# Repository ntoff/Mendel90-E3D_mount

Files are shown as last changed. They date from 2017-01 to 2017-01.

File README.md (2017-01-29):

# Mendel90 E3D Direct Drive Mount

Printable mount for an E3D hotend on a Mendel90 reprap printer.

Uses some of the parts from the Orca printer's extruder and mount system
http://reprap.org/wiki/Orca
http://reprap.org/wiki/Orca_alternative_build

Note: Screw length may vary depending how thick you tell it to make the plates.
You may be required to shave some off one of the bolts if it interferes with the E3D fan
since bolts of odd lengths (like M4 x 13mm) may not exist.

## BOM:

## Idler / feeder bit:
M4 x 70 (x4)
M4 washers (x8)
4.5 - 5mm ID springs 20mm long
M4 x 45 (x2)
M4 nyloc nuts (x2)

## Idler bearing holder
M4 rod approx. 18mm long
M4 washers (x2)
Bearing w/ 4mm hole 13mm OD 5mm wide
M4 nyloc nuts (x4)

## Motor mount:
M3 x8 (x4)
M4 x15 (x1)
M3 washers (x4)
M4 washers (x2)
M4 nyloc nuts (x1)

## Base:
M4 x 15 countersunk (x4)
M4 washers (x2)
M4 nyloc nuts (x4)

driverholder.STL vs extruder guide2.stl: driverholder includes an extra mount point on the base, makes it stronger but also makes it harder to remove / mount. 
I suggest sticking with the guide2 version.

Obviously don't print the shaft, bearing, or bearing real files, they were just for reference for design, I took some artistic liberty with the size of the bearing,
stl dimensions are not an accurate representation of any actual bearing sizes.

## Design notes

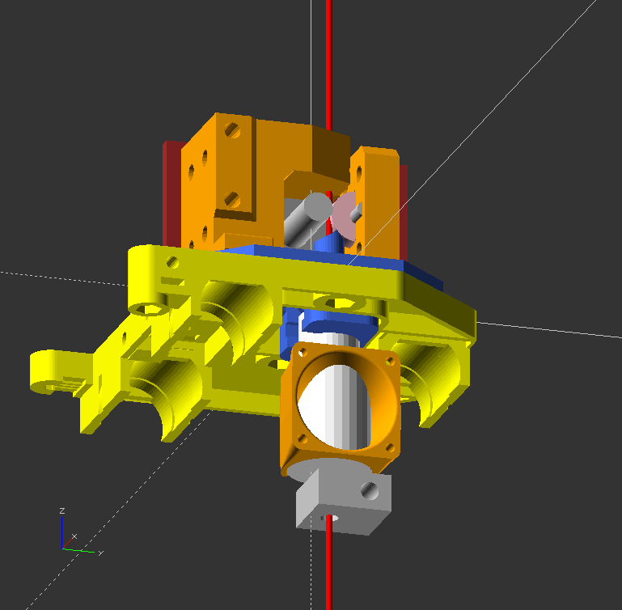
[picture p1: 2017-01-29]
e3d mount.png

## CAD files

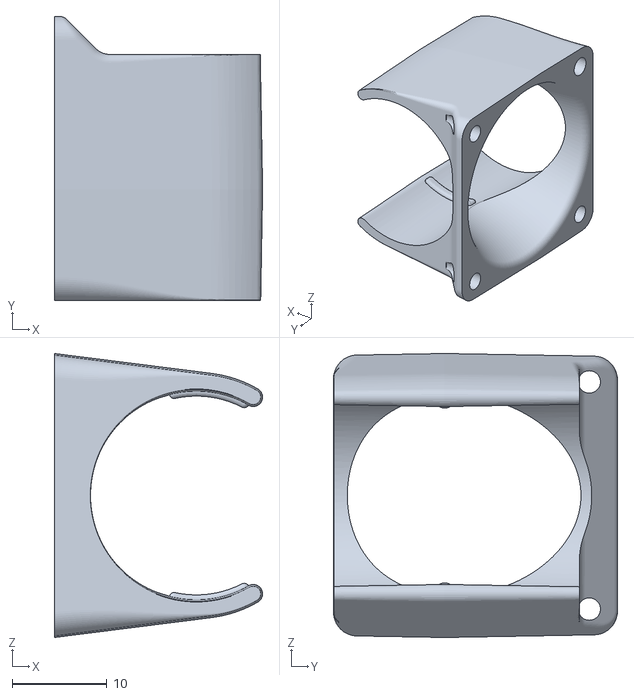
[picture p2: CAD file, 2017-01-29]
V6.6_Duct.stl
22.0 x 30.0 x 30.0

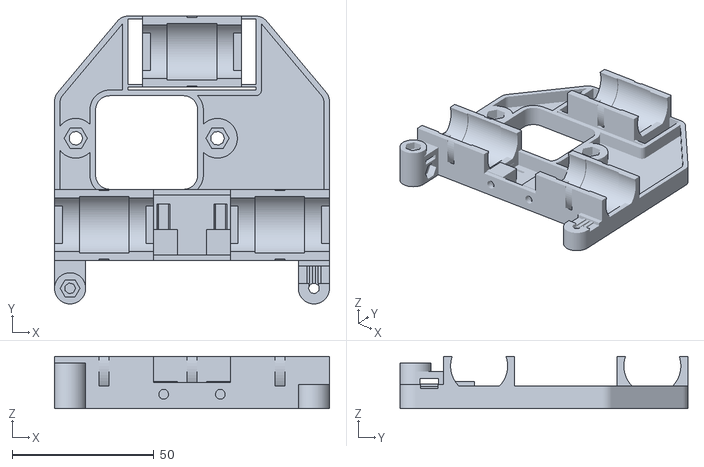
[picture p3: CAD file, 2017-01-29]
x_carriage.stl
97.0 x 101.5 x 18.4

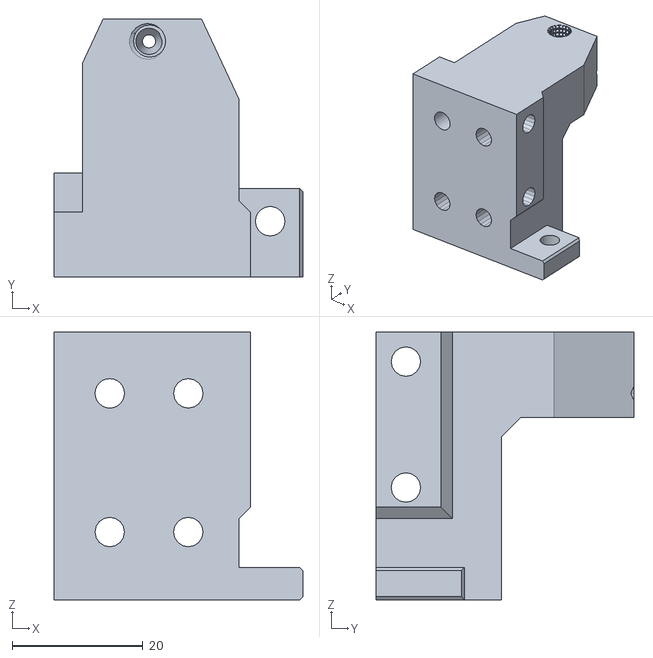
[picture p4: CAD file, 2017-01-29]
driverholder.STL
38.0 x 39.4 x 40.9

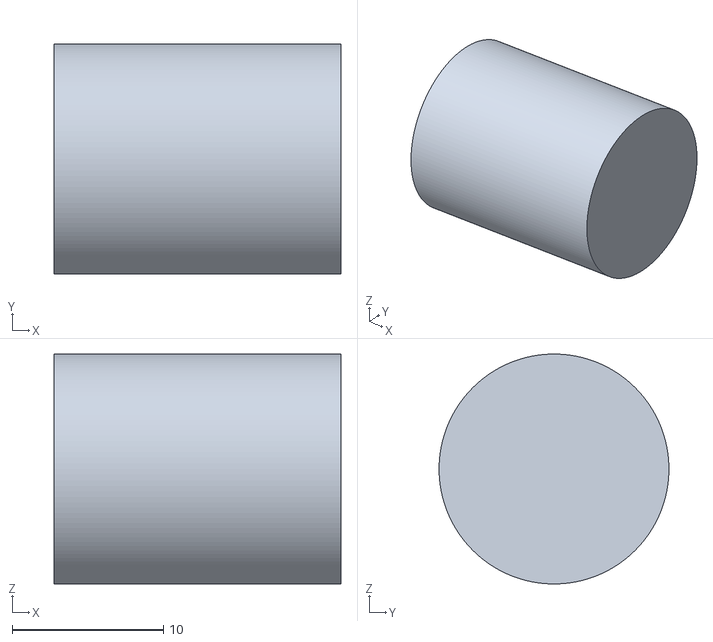
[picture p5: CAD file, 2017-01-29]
idler_bearing.stl
19.0 x 15.2 x 15.2

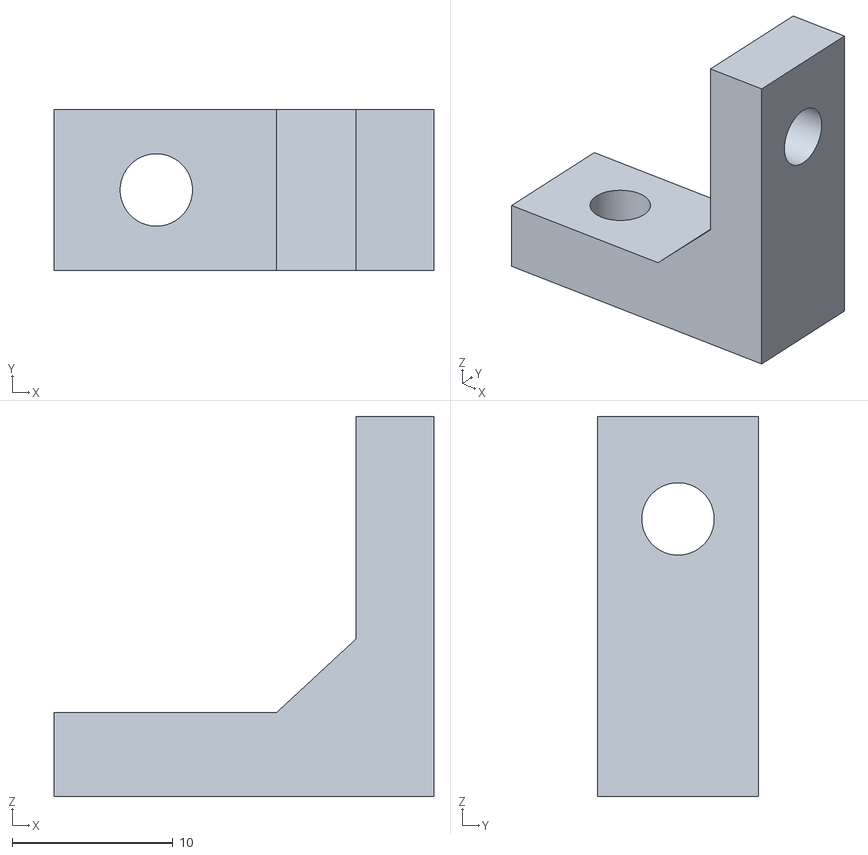
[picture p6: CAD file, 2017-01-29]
extruder_corner.stl
23.6 x 10.0 x 23.7

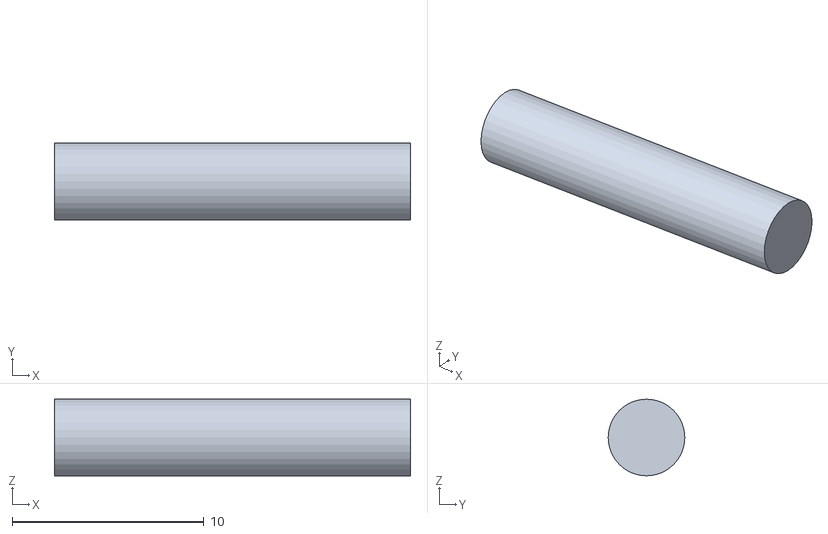
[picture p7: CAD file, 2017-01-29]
idler_shaft.stl
18.6 x 4.00 x 4.00

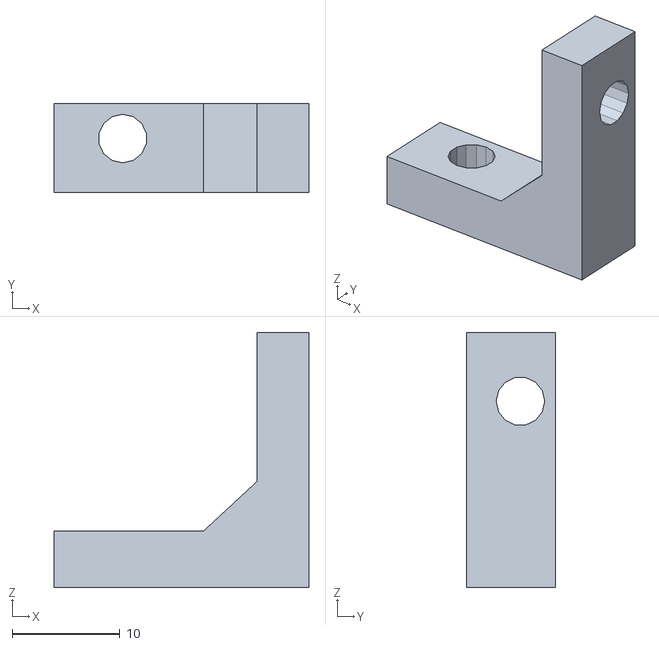
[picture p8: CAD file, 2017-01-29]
extruder_corner_shaved.stl
23.6 x 8.25 x 23.7

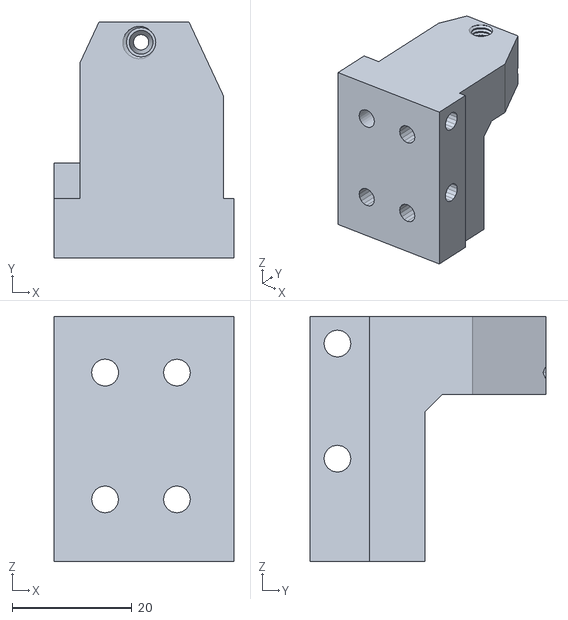
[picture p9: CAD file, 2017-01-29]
extruder guide2.stl
30.0 x 39.4 x 40.9

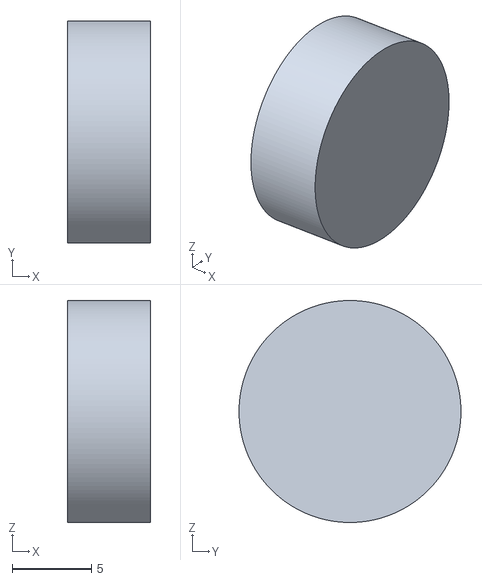
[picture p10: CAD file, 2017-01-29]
idler_bearing_real.stl
5.24 x 14.0 x 14.0

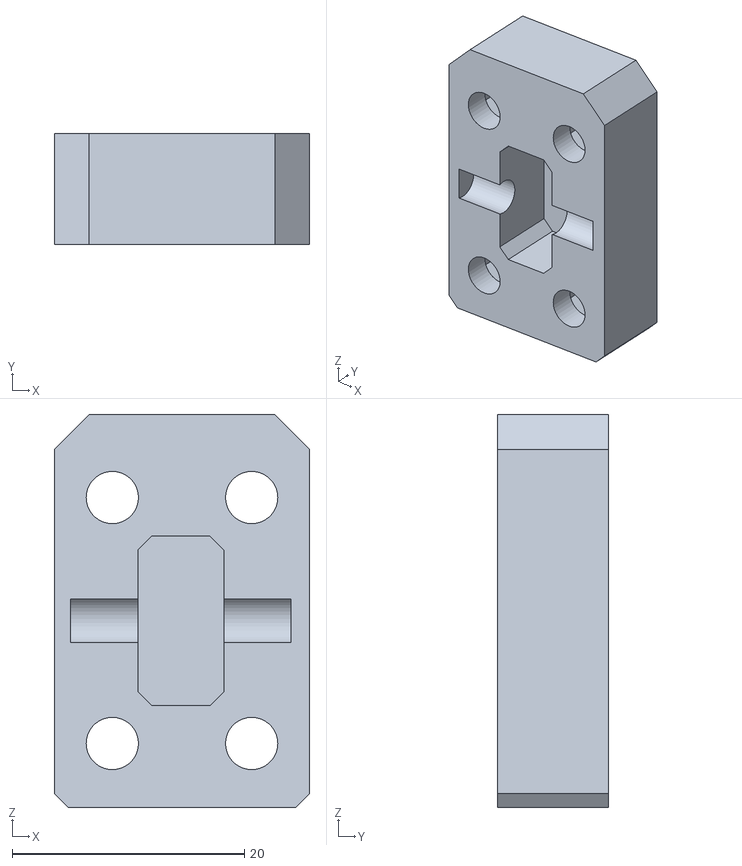
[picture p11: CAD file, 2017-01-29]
idler.stl
22.0 x 9.52 x 33.8

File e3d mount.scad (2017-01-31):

include<nema17.scad>
/*E3D mount for a mendel90
F5 to compile it for viewing the assembled assembly
F6 to compile it with just the mount plate, base plate, and filament guide to see orientation of parts

change print variable to 1 and F6 to compile for printing

note: Only openscad parts are compiled for printing, imported STLs won't show up but can be manually
added to your slicer. DO NOT PRINT THE X CARRIAGE, included x carriage is only for design reference,
the x carriage generated for your machine should be used as long as the holes all line up, check by
replacing the included x carriage with your own.
*/

//CHANGE THIS TO 1 TO COMPILE FOR PRINTING
print=0;
$fn=32;
plate_thickness=5;
upright_thickness=4;
offset=5; //moves the motor left and right for different sized drive wheels
x=18.5;
y=35;
y2=31;
plate_height=43;
filament_hole_size = 17; //size of the hole in the base plate, NOT the size of your filament
bowden_tube_dia=4.5; //diameter of the PTFE liner in the e3d

module extras(){
    %color("red")translate([0,5,-100])cylinder(d=1.75,h=200); //filament for reference
    /**/
    %color("white")translate([0,5,-42.7-3]){
        cylinder(d=22.3,h=26);
        cylinder(d=16,h=42.7);
        translate([0,0,-7.1])cylinder(d=3,h=7.1);
        translate([0,0,-7.1])cylinder(d=3,h=11.5);
        } //e3d heatsink for reference
    %color("silver")translate([0,4+5,-42.7-3-8])
        difference(){
            cube([20,20,10],center=true);
            translate([0,4,0])rotate([0,90,0])cylinder(d=5,h=21,center=true);
            translate([0,-4,0])cylinder(d=5,h=11,center=true);
        }
    /**/
    %translate([-18.52,-0+5-31/2-offset,41.6-(5-plate_thickness)])rotate([0,90,0])nema(nema_height=3,shaft_dia=8);
    %color("red")translate([-18.5,-31.45,plate_thickness])import("extruder_corner_shaved.stl");
    %color("red")translate([-18.5,21.5,plate_thickness])import("extruder_corner.stl");
    %color("orange")translate([18.5,-28+5.5+2.9,plate_thickness])rotate([0,0,0])import("idler.stl"); //idler bearing holder
    %color("silver")translate([18.5,-28+5.5+2.9,plate_thickness])rotate([0,0,0])import("idler_shaft.stl"); //idler bearing holder
    %color("pink")translate([18.5,-28+5.5+2.9,plate_thickness])rotate([0,0,0])import("idler_bearing_real.stl"); //idler bearing holder
    /*
        Comment out ONE of these to make more sense of it all
        either the one with or without the extra tab is needed but not both.
        There's not much difference other than one extra bolt.
    */
    //filament guide with extra mount tab
    //%color("orange")translate([18.5,-28+5.5,plate_thickness])rotate([0,0,0])import("driverholder.stl"); 
    //filament guide without extra mount tab
    %color("purple")translate([18.5,-28+5.5,plate_thickness])rotate([0,0,0])import("extruder guide2.stl"); 
    %color("yellow")translate([0,0,0])rotate([0,180,0])import("x_carriage.stl");
    /*
        E3d fan duct for reference, comment out TWO of them to leave the one you want
    */
    //front facing
    //%color("red")translate([0,5,-19.7])rotate([-90,0,90])import("V6.6_Duct.stl");  
    //right facing
    %color("orange")mirror([1,0,0])translate([0,5,-46])rotate([90,0,0])import("V6.6_Duct.stl"); 
    //left facing
    //%color("green")translate([0,5,-46])rotate([90,0,10])import("V6.6_Duct.stl");
}

module e3d(){
    extra=8;
    hull(){
        translate([0,5,0])rotate([180,0,0])cylinder(d=16.5,h=4);
        translate([0,-5,0])rotate([180,0,0])cylinder(d=16.5,h=4);
    }
    translate([0,5,-3.95+extra])rotate([180,0,0])cylinder(d=12.2,h=6+extra);
    hull(){
        translate([0,5,-3.95+extra])rotate([180,0,0])cylinder(d=11,h=6+extra);
        translate([0,-5,-3.95+extra])rotate([180,0,0])cylinder(d=13,h=6+extra);
    }
    hull(){
        translate([0,5,-10])rotate([180,0,0])cylinder(d=16.5,h=2);
        translate([0,-5,-10])rotate([180,0,0])cylinder(d=16.5,h=2);
    }
}

module baseplate(){
    color("RoyalBlue")difference(){
        union(){
            linear_extrude(plate_thickness)
               polygon( points=[[-45,-y],[-60,-15],[-60,10],[-43,y2],[17,y2],[30,y2-15],[30,-y+10],[20,-y]]);
            minkowski(){
            translate([-25/2,10,0])rotate([180,0,0])cube([25,10,5]);
                rotate([180,0,0])cylinder(d=9,h=5);
            }
            //translate([0,5,0])rotate([180,0,0])cylinder(d=20,h=10,$fn=$fn*2);
        }

        //mounting holes
        translate([-25,0,plate_thickness-2.9])cylinder(d1=5,d2=9,h=3); //countersink
        translate([25,0,plate_thickness-2.9])cylinder(d1=5,d2=9,h=3); //countersink
        translate([-25,0,-1])cylinder(d=5,h=plate_thickness); 
        translate([25,0,-1])cylinder(d=5,h=plate_thickness);
        //end mounting holes
            
        translate([18.5,-28+5.5,1])cylinder(d=5,h=plate_thickness); //guide mount hole
        translate([18.5,-28+5.5,-0.1])cylinder(d1=9,d2=5,h=3); //guide mount hole countersink
        translate([-35.7,-26.25,1])cylinder(d=5,h=plate_thickness); //motor 90 degree bracket mount hole
        translate([-35.7,26.25,1])cylinder(d=5,h=plate_thickness); //motor 90 degree bracket mount hole
        translate([-35.7,-26.25,-0.1])cylinder(d1=9,d2=5,h=3); //motor 90 degree bracket mount hole countersink
        translate([-35.7,26.25,-0.1])cylinder(d1=9,d2=5,h=3); //motor 90 degree bracket mount hole countersink
        
        translate([0,5,+plate_thickness/2])cylinder(d=filament_hole_size,h=plate_thickness+0.5,center=true,$fn=32); //filament hole
        translate([0,0,-3])e3d();

    }
}

module filament_inlet(){
    clearance = 0.4;
    color("RoyalBlue")
    difference(){
        union(){
            translate([0,5,+plate_thickness/2])cylinder(d=filament_hole_size-clearance,h=plate_thickness+0.5,center=true,$fn=32); //filament hole
            translate([0,5,0])cylinder(d=8,h=24,center=false,$fn=32); //filament hole
        }
        translate([18.5,-28+5.5+2.9,plate_thickness])rotate([0,0,0])import("idler_bearing.stl"); //idler bearing holder
        translate([-18.52,-0+5-31/2-offset,40.6])rotate([0,90,0])nema(nema_height=3,shaft_dia=15);
        translate([0,5,0])cylinder(d=bowden_tube_dia,h=25,center=false,$fn=32); //filament hole
        translate([0,5,+plate_thickness/2-0.76])cylinder(d1=filament_hole_size-clearance-2,d2=bowden_tube_dia,h=plate_thickness+0.5-1.5,center=true,$fn=32); //filament hole
    }
}

module nema_mount(){
difference(){
    union(){
        
        color("brown")translate([0,0,plate_thickness])
            linear_extrude(plate_height)
                polygon( points=[[-x,-y],[-x,y2],[-x+upright_thickness,y2],[-x+upright_thickness,-y]]);
        }
     
    translate([-18.52,-0+5-31/2-offset,41.6-(5-plate_thickness)])rotate([0,90,0])nema(nema_height=10);
    //bolt holes
    color("green") translate([0,-26.44,22.17-(5-plate_thickness)])rotate([0,90,0])cylinder(d=5,h=100,center=true);
    color("green") translate([0,26.44,22.17-(5-plate_thickness)])rotate([0,90,0])cylinder(d=5,h=100,center=true);
    color("green") translate([0,-26.44,22.17+19.25-(5-plate_thickness)])rotate([0,90,0])cylinder(d=5,h=100,center=true);
    //zip tie hole for holding the cables, comment out if you don't want it
    color("green") translate([0,26.44,22.17+19.25-(5-plate_thickness)])rotate([0,90,0])cylinder(d=5,h=100,center=true);
}
}

if (print == 1){
    translate([0,0,plate_thickness])rotate([180,0,0]) 
        baseplate();
    translate([-10,35,-x+upright_thickness])rotate([0,90,90]) 
        nema_mount();
    translate([-8,56,0.25]) 
        filament_inlet();
}else {
    baseplate();
    nema_mount();
    filament_inlet();
    extras();
    }

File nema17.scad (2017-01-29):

nema_height=10;
shaft_dia=6;
module nema(nema_height,shaft_dia){
    echo("Note: Nema is designed to be differenced out of something, dimensions of screws and shaft are larger than actual");
linear_extrude(nema_height){
    hull(){
        translate([0,0-2,0])circle(d=3.5,$fn=16);
        translate([0,02,0])circle(d=3.5,$fn=16);
    }
    hull(){
        translate([31,0-2,0])circle(d=3.5,$fn=16);
        translate([31,02,0])circle(d=3.5,$fn=16);
    }
    hull(){
        translate([31,31-2,0])circle(d=3.5,$fn=16);
        translate([31,31+2,0])circle(d=3.5,$fn=16);
    }
    hull(){
        translate([0,31-2,0])circle(d=3.5,$fn=16);
        translate([0,31+2,0])circle(d=3.5,$fn=16);
    }
}
linear_extrude(nema_height)hull(){
    translate([31/2,31/2-2,0])circle(d=25);
    translate([31/2,31/2+2,0])circle(d=25);
}
color("Silver")translate([31/2,31/2,0])cylinder(d=shaft_dia,h=25,$fn=64); //motor shaft


color("DarkSlateGray")translate([(31-42)/2,(31-42)/2,-42])cube(42); //motor body
}

//rotate([0,90,0])
//nema(nema_height=3,shaft_dia=15);

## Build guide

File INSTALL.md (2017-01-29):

Print all parts with your favourite slicer, supports should be used for the base plate.

Note: Do _NOT_ use the x carriage included here, it is *only* for reference during design and is from
the Mendel90 Sturdy variant, the carriage generated for your particular machine should be used provided the hole width is
the same (check by importing your own x carriage).

Insert 2 M4 countersunk bolts up from the bottom of the base (the bottom is the part where the e3d mounts to) and bolt the 90 degree
supports to the base plate, use an m4 washer and nyloc nut.

Screw the motor to the mount plate with the short side (side with the holes closest to the edge) facing the back of the x carriage using the M3 x 8 screws and M3 washers.

Loosely fit your filament drive wheel to the motor shaft, insert the filament guide into the base (**don't** glue it in), sit the motor + mount plate on the base and adjust the position
of the filament drive wheel to line up with the filament guide.

Assemble the E3D as per the E3D instructions (note: This mount was designed for the size of a genuine E3D v6), putting in the little black PTFE liner clip but NOT the liner itself just yet,
and leave the fan shroud off for now.

Push the E3D into the base plate clip

Insert a length of PTFE liner into the hotend, long enough to reach the top of the filament guide, sit the filament guide in the base and trim the PTFE tube with a sharp knife to match the 
profile of the guide. (note: future removal of the liner is still possible as long as you don't ever glue in the filament guide.)

Put the base plate + e3d assembly onto your x carriage and secure with M4 x 15 countersunk bolts and nylock nuts. One of them may interfere with the E3D fan depending on the shroud orientation
, thickness of the base plate, and length of available screws, trimming of one bolt may be necessary.

Use 1x M4 x 15 bolt to secure the back of the mount plate to the 90 degree upright, secure with M4 washer and nyloc nut

Secure the filament inlet / idler mount with 2x M4 x 45 bolts, washers, and nyloc nuts.

Insert an M4 rod into the bearing, an M4 washer either side and insert into the idler bearing holder.

Attach idler bearing holder using M4 x 70 bolts, a washer either side of the spring and M4 nyloc nuts.
(I just use 2x M4 x 70 bolts here, 4 is a bit overkill but that was the original design so it's up to you.)

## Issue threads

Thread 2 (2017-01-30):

changing of upright_thickness doesn't work properly

ntoff, 2017-01-30:
It adjusts the plate thickness but doesn't move any brackets or holes to compensate

ntoff, 2017-01-31:
bodge fix in https://github.com/ntoff/Mendel90-E3D_mount/tree/dev/nema_plate works but ugly (quick fix)

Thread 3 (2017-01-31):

Extra hole for filament idler mount not parametric

ntoff, 2017-01-31:
Increasing base thickness won't increase the hole depth and results in a blank hole.

ntoff, 2017-01-31:
Fixed

Closed 2017-01-31.

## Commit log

2017-01-29 initial upload
    [V6.6_Duct.stl, driverholder.STL, e3d mount.scad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]
2017-01-31 fix for issue #3
    whoops, forgot to make it parametric, fixed now (I hope, seems to be)
    and added information to comments about which part is the countersunk
    bit
    [e3d mount.scad]
